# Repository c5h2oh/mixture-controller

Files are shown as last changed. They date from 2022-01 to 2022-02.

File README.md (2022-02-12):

# mixture-controller
RC engine mixture controller.

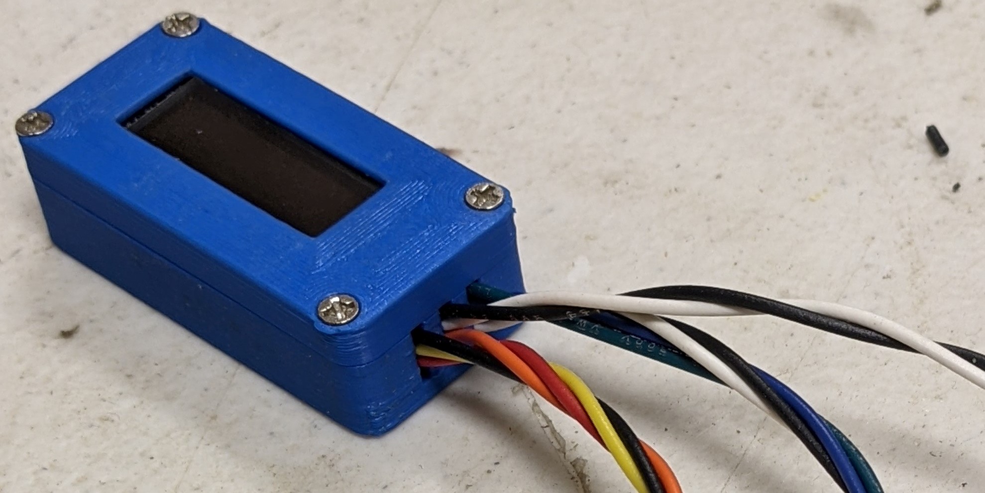
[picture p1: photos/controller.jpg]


This controller works with a stihl solenoid part number 0000 120 5111 and a custom solenoid housing (https://github.com/raleighcopter/mixture-controller/blob/main/photos/solenoid%20housing.pdf) to modulate gasoline flow to a conventional methanol carburator. This allows us to generate a custom fuel mixture curve on our transmitter that is slaved to the throttle channel output. The result is that we can vary the fuel:air mixture across the entire throttle range to make the engine run near stoichiometric fuel:air ratio at idle, full throttle, and every point in between. Without the solenoid and controller, our methanol engines run extremely rich in the middle. 

The controller takes an RC channel and maps a 1000 uS - 2000 uS channel pulse to a PWM solenoid pulse. Additionally, the controller measures atmospheric pressure and temperature and adjusts the fuel amount to maintain the ideal mixture regardless of the weather or altitude (which constantly changes as we fly our models). We have engines that were tuned at 85 degrees F that run just as well at 35 degrees F without touching the needles. 

I currently have my OS FT120-ii and Saito FA72 converted and Bert (the man behind the idea who designed the solenoid housing) has engines ranging from an asp 0.30 four stroke up to an ASP 1.6 boxer and a larger radial converted and running well. This conversion has been used on 2 stroke engines, 4 stroke engines, single  and twin cylinder engines and radial multi-cylinder engines.

I built the controller using a seeduino Xiao an IRLD110pbf MOSFET, a 2.2k resistor, a diode, a bmp280, and optionally, a 128x32 oled display and I've tested it on 4s NiMH and 2s LiFePo. Power comes in on the power and ground pads on the back of the Xiao. 

If you're powering your controller with a 2s LiFePo battery, wire a 1n4003 diode or something similar in the red wire before feeding power to the power pad or the Vcc pin. if you're powering your controller with a 4S NiMh, omit the diode.

The solenoid, bmp280, and optional display grab 3.3 volts from the Xiao's 3.3v pin. The MOSFET is wired to D3 and the RC channel is wired to D2. There's only 1 ground pad on the back and one ground pin so I doubled up on the pad on the back because I need 3 grounds.

I wired a 2.2k resistor across the MOSFET's gate and source (an 0805 smt resistor works really well here but a 1/8 watt resistor also works) and added a short piece of wire to those pins before I slipped some heat shrink over the separate pins. I soldered the wire that runs to the solenoid to the MOSFET's drain, trimmed the pins and then covered the entire MOSFET with heat shrink. After it was covered with heat shrink, I soldered the wire from the MOSFET's gate to D3 and the wire from the MOSFET's source to ground.

SDA and SCL from the bmp280 go to D4 and D5 and the optional display also uses these connections. if you measure resistance of about 10k between SDO and ground on the bmp280 it has a base address of 0x76. otherwise it has a base address of 0x77 and you need to change the base address at the top of the controller code. 

If you're building this with an oled display, wire the display to the same 4 points that the bmp280 is connected: 3.3v, ground, SDA, and SCL. You can wire it in parallel or in series with the bmp280.

if you're using this with an opentx transmitter and want s.port data, connect your s.port to pin 0 of the Xiao.

ebay/china is the least expensive source for bmp280 sensors at about $1 each and 128x32 oled displays at about $2.50. Be aware that we've seen fairly high failure rates on the China sourced bmp280 boards. As a result, the solenoid will signal a failed sensor at startup by buzzing for half a second and then remaining quiet for another half second and repeating indefinitely..

you'll need to install a few libraries in the arduino IDE: adafruit bmp280, adafruit ssd1306, adafruit GFX library and the frsky s.port sensor library by herman kruisman. you'll also need to add the seeeduino xiao board definition using the board manager.

build photos as well as parts lists and assembly instructions are on the wiki at https://github.com/raleighcopter/mixture-controller/wiki

Contact me at d.a.taylor.pe@gmail.com

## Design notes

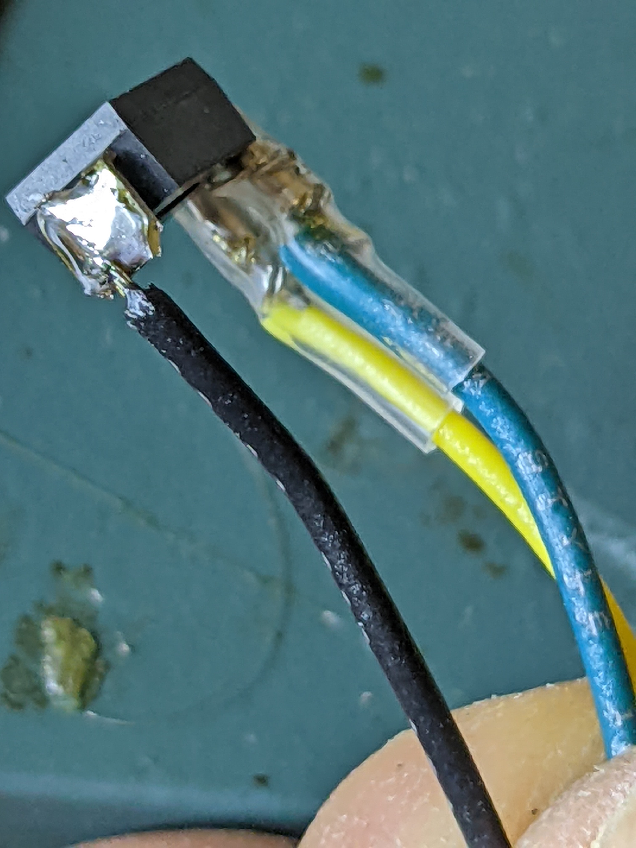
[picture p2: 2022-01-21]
photos/zero_11.jpg

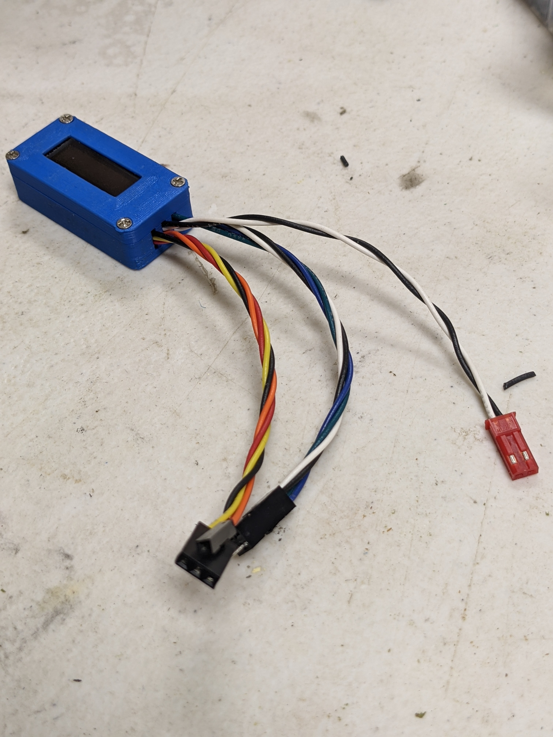
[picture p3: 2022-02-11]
photos/c1.jpg

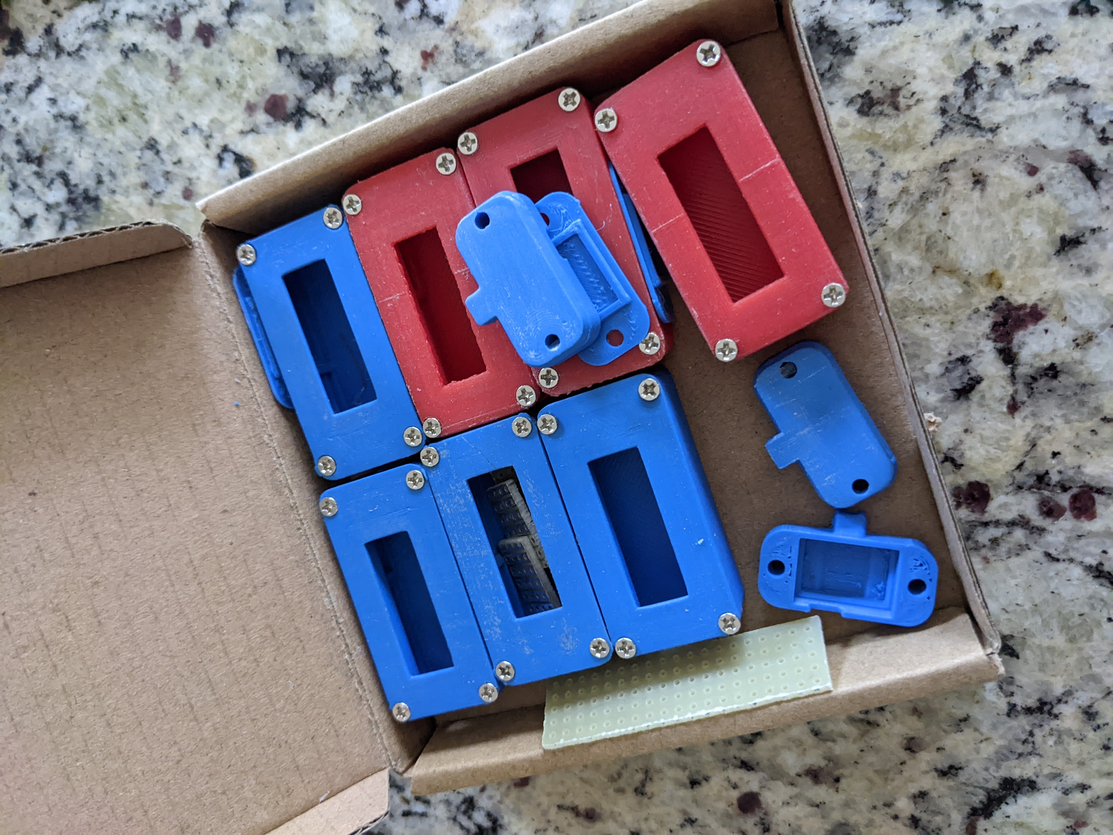
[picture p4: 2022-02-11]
photos/c2.jpg

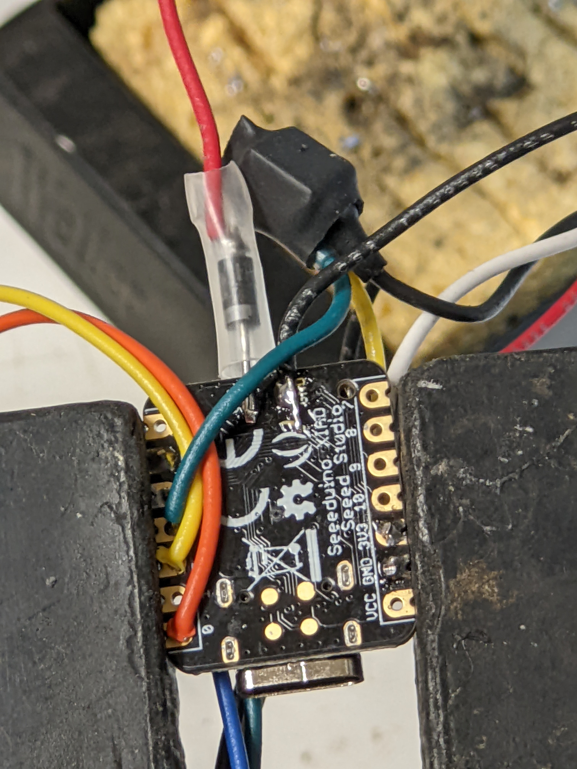
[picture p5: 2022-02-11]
photos/c12.jpg

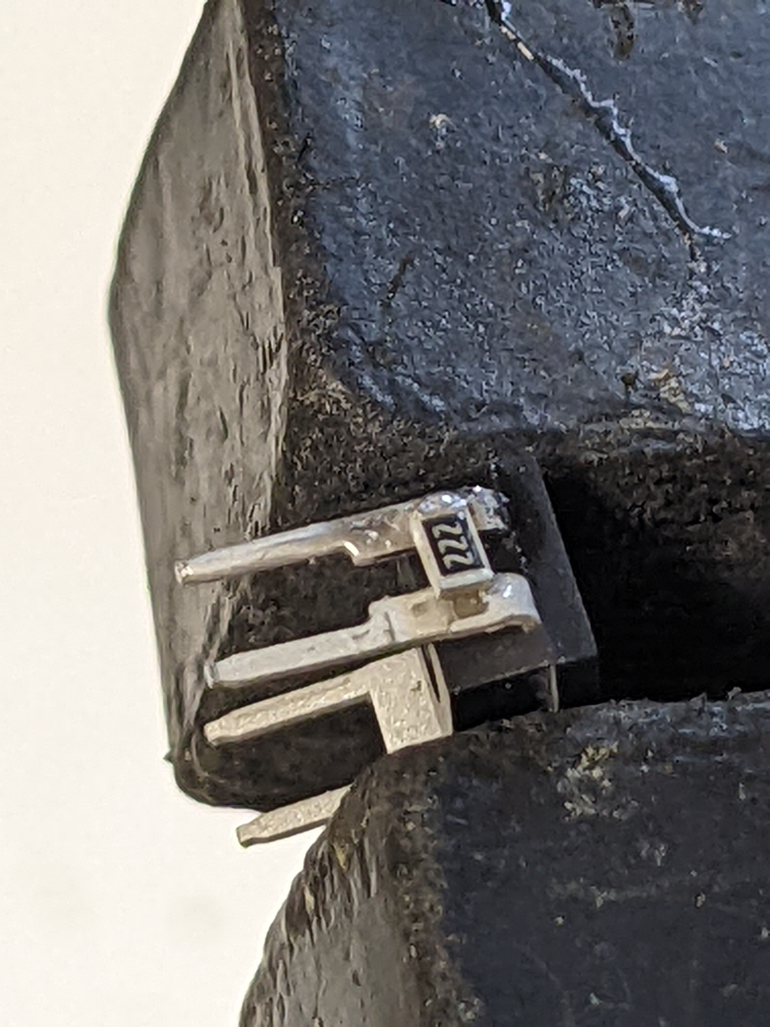
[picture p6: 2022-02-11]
photos/c4.jpg

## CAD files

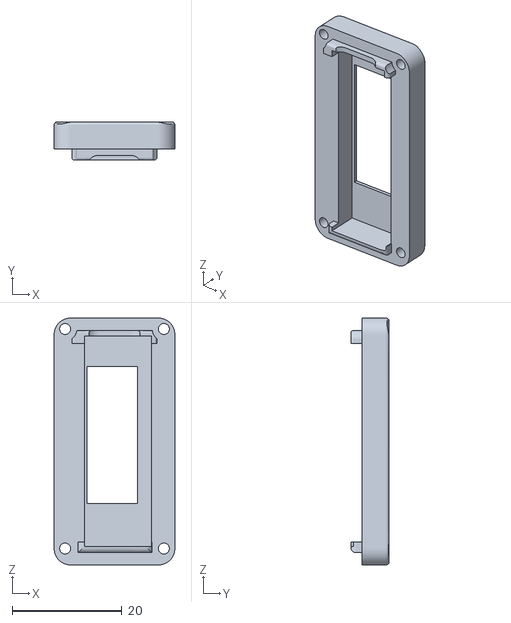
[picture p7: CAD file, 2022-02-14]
case_files/OLED lid.stl
22.0 x 7.00 x 45.0

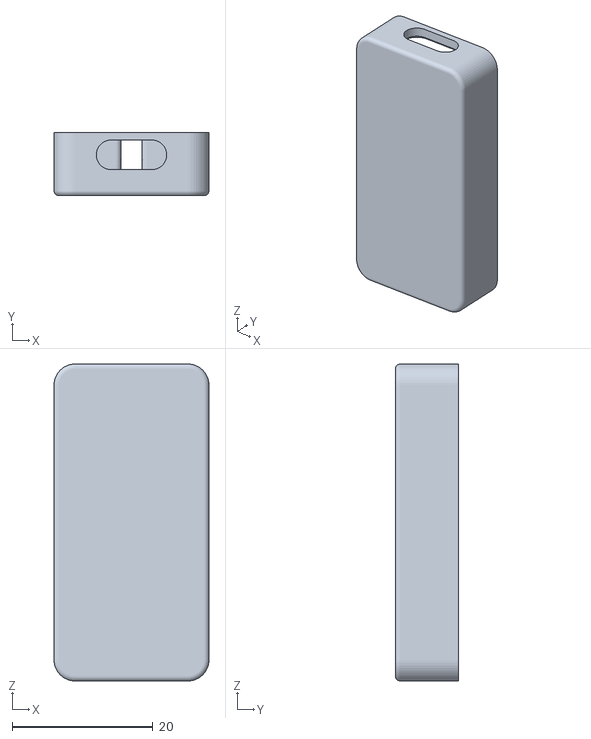
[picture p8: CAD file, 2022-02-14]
case_files/AMC case v9.stl
22.0 x 9.00 x 45.0

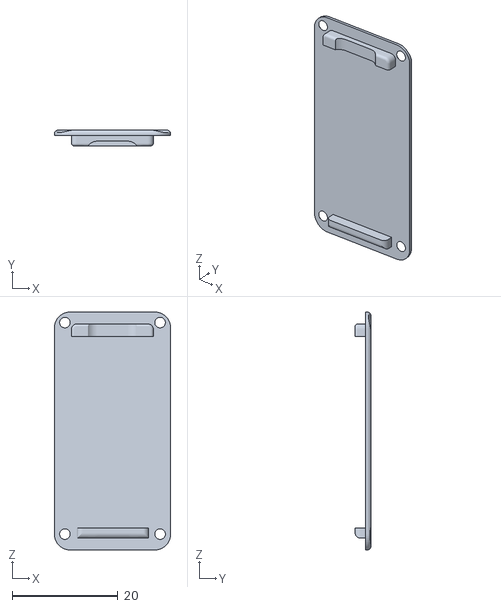
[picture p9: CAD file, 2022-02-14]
case_files/No OLED Lid.stl
22.0 x 3.00 x 45.0

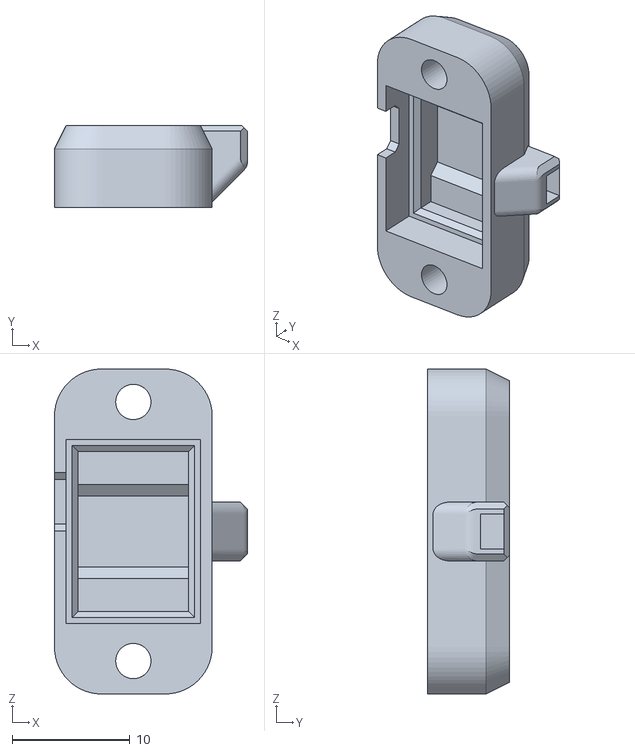
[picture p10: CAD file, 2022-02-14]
case_files/BMP280 Case.stl
16.4 x 7.00 x 27.6

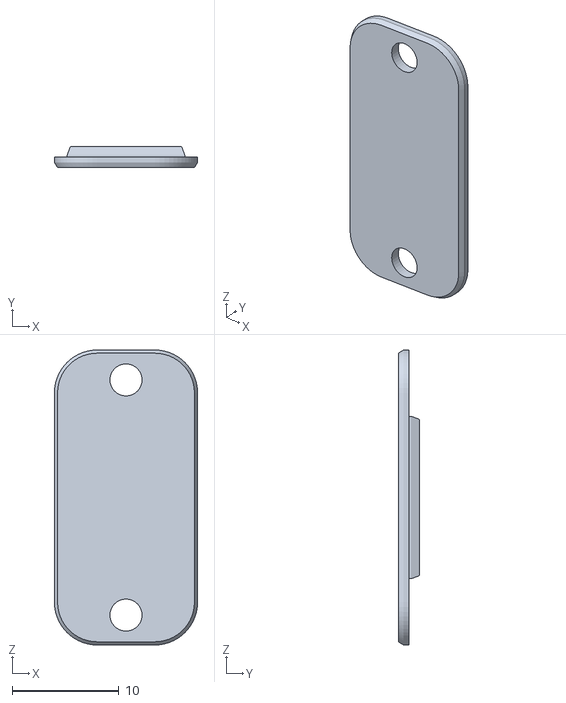
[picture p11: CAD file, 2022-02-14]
case_files/BMP280 cover.stl
13.4 x 2.00 x 27.6

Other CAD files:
case_files/AMC case.f3d

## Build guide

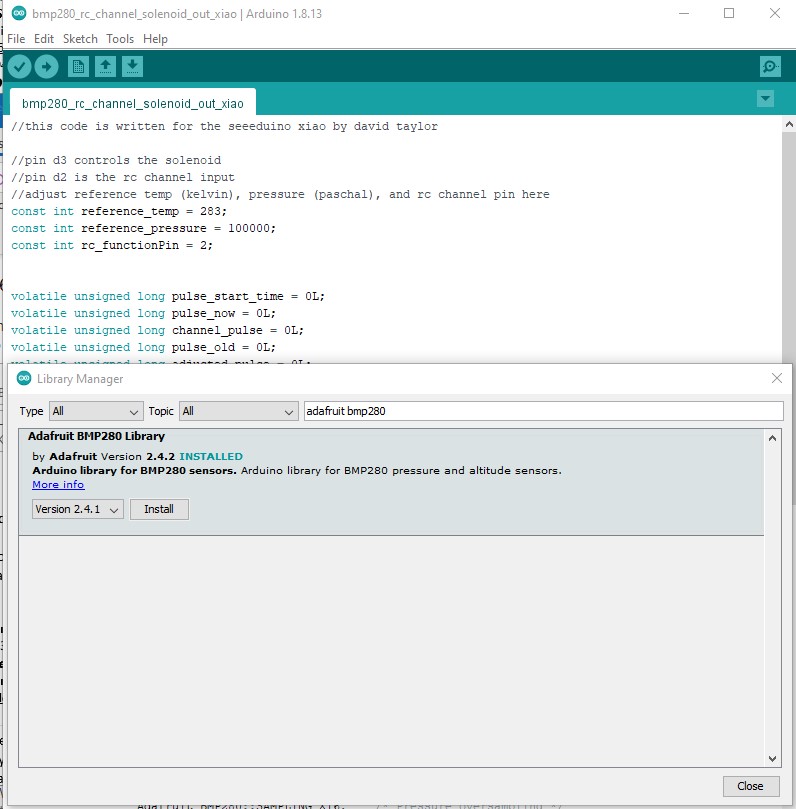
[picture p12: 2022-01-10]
photos/library install.jpg

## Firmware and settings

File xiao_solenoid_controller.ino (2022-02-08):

//this code is written for the seeeduino xiao by david taylor and released under the 
//GNU general public license V3.0. Permissions of this strong copyleft license are 
//conditioned on making available complete source code of licensed works and modifications,
//which include larger works using a licensed work, under the same license. Copyright and 
//license notices must be preserved. Contributors provide an express grant of patent rights.
// Also, Gary Cee from rcgroups is a douchebag

//pin d3 controls the solenoid
//pin d2 is the rc channel input
//adjust reference temp (kelvin), pressure (paschal), and rc channel pin here
const int reference_temp = 283;
const int reference_pressure = 100000;
const int rc_functionPin = 2;

//OLED addresses are 0x3C or 0x3D
#define OLED_ADDR   0x3C

//BMP280 addresses are 0x76 or 0x77
#define BMP280_ADDR   0x76

//****************************************************************************************
// **********************  DO NOT EDIT ANYTHING BELOW THIS LINE  *************************
//****************************************************************************************

unsigned long old_time;
int update_display;
const long display_interval = 1000; 
volatile unsigned long pulse_start_time = 0L;
volatile unsigned long pulse_now = 0L;
volatile unsigned long channel_pulse = 0L;
volatile unsigned long pulse_old = 0L;
volatile unsigned long adjusted_pulse = 0L;
volatile unsigned long solenoid_pulse = 0L;
volatile unsigned long usable_pulse = 0L;
int channel;
int bmp_error = 0;
char _buffer[9];

#include <SPort.h> 
#include <Wire.h>
#include <Adafruit_GFX.h>      // include Adafruit graphics library
#include <Adafruit_SSD1306.h>  // include Adafruit SSD1306 OLED display driver
#include <Adafruit_BMP280.h>   // include Adafruit BMP280 sensor library

Adafruit_BMP280 bmp; // I2C
Adafruit_SSD1306 display(-1);  // initialize Adafruit display library, share reset with xiao reset

SPortHub hub(0x12, 0);                    //Hardware ID 0x12, Software serial pin 0
CustomSPortSensor intake_temperature(getSensorData);  //Sensor with a callback function to get the data
CustomSPortSensor intake_pressure(getSensorData1);  //Sensor with a callback function to get the data
CustomSPortSensor compensation_ratio(getSensorData2);  //Sensor with a callback function to get the data
CustomSPortSensor solenoid_command(getSensorData3);  //Sensor with a callback function to get the data

void setup() {

  hub.registerSensor(intake_temperature);          //Add sensor to the hub
  hub.registerSensor(intake_pressure);             //Add sensor to the hub
  hub.registerSensor(compensation_ratio);          //Add sensor to the hub
  hub.registerSensor(solenoid_command);            //Add sensor to the hub


  hub.begin();                            //Start listening for s.port data

// initialize the SSD1306 OLED display with I2C address = 0x3C
  display.begin(SSD1306_SWITCHCAPVCC, OLED_ADDR);
// clear the display buffer.
  display.clearDisplay();
  display.setTextSize(1);   // text size = 1
  display.setTextColor(WHITE, BLACK);  // set text color to white and black background
  
//uncomment the next line to debug  
//SerialUSB.begin(115200);

  pinMode(rc_functionPin, INPUT);
  attachInterrupt(rc_functionPin, RCpinread, CHANGE);

  if (!bmp.begin(BMP280_ADDR, BMP280_CHIPID)) {
//  SerialUSB.println(F("Could not find a valid BMP280 sensor, check wiring or try a different address!"));
  bmp_error = 1;
  }
  
  bmp.setSampling(Adafruit_BMP280::MODE_NORMAL,     /* Operating Mode. */
                  Adafruit_BMP280::SAMPLING_X2,     /* Temp. oversampling */
                  Adafruit_BMP280::SAMPLING_X16,    /* Pressure oversampling */
                  Adafruit_BMP280::FILTER_X16,      /* Filtering. */
                  Adafruit_BMP280::STANDBY_MS_500); /* Standby time. */

//setup timer regisiters
  pinMode(3, OUTPUT);
  REG_GCLK_GENDIV = GCLK_GENDIV_DIV(1000) |       // Divide the main clock down by some factor to get generic clock
                    GCLK_GENDIV_ID(4);            // Select Generic Clock (GCLK) 4
  while (GCLK->STATUS.bit.SYNCBUSY);              // Wait for synchronization

  REG_GCLK_GENCTRL = GCLK_GENCTRL_IDC |           
                     GCLK_GENCTRL_GENEN |         // Enable GCLK4
                     GCLK_GENCTRL_SRC_DFLL48M |   // Set the 48MHz clock source
                     GCLK_GENCTRL_ID(4);          // Select GCLK4
  while (GCLK->STATUS.bit.SYNCBUSY);              // Wait for synchronization

// Enable the port multiplexer for the digital pin. 
  PORT->Group[g_APinDescription[3].ulPort].PINCFG[g_APinDescription[3].ulPin].bit.PMUXEN = 1;
  
//Connect the TCC0 timer to digital output - port pins are paired odd PMUO and even PMUXE 
  PORT->Group[g_APinDescription[2].ulPort].PMUX[g_APinDescription[2].ulPin >> 1].reg = PORT_PMUX_PMUXO_E; // | PORT_PMUX_PMUXE_F;

// Feed GCLK4 to TCC0 and TCC1
  REG_GCLK_CLKCTRL = GCLK_CLKCTRL_CLKEN |         // Enable GCLK4 to TCC0 and TCC1
                     GCLK_CLKCTRL_GEN_GCLK4 |     // Select GCLK4
                     GCLK_CLKCTRL_ID_TCC0_TCC1;   // Feed GCLK4 to TCC0 and TCC1
  while (GCLK->STATUS.bit.SYNCBUSY);              // Wait for synchronization

//Set for Single slope PWM operation: timers or counters count up to TOP value and then repeat
  REG_TCC1_WAVE |= TCC_WAVE_WAVEGEN_NPWM;        // Reverse the output polarity on all TCC0 outputs
  while (TCC1->SYNCBUSY.bit.WAVE);               // Wait for synchronization
 
  REG_TCC1_PER = 6144;                           // This sets the rate or frequency of PWM signal 
  while (TCC1->SYNCBUSY.bit.PER);                // Wait for synchronization
  
// Set the PWM signal to output 50% duty cycle initially 
  REG_TCC1_CC1 = 3072;                           // this sets the pwm duty cycle. values from 0 6145 are valid. 
  while (TCC1->SYNCBUSY.bit.CC1);                // Wait for synchronization

// Set prescaler and enable the outputs
  REG_TCC1_CTRLA |= TCC_CTRLA_PRESCALER_DIV1 |    // Divide GCLK4 by 1
                    TCC_CTRLA_ENABLE;             // Enable the TCC0 output
  while (TCC1->SYNCBUSY.bit.ENABLE);              // Wait for synchronization



}

//############################################################################

void loop() {

while(bmp_error == 1) {
  display.clearDisplay();
  display.setCursor(0, 0);
  display.setTextSize(2);
  display.println("  SENSOR");
  display.println("  ERROR");
  display.display();  
  REG_TCC1_CC1 = 3072;
  delay(500);
  REG_TCC1_CC1 = 0;
  delay(500);  
}
  
  hub.handle();                           //Handle new s.port data
  
//adjust for temp and pressure  
    adjusted_pulse = (usable_pulse * (reference_temp/(bmp.readTemperature()+273)*(bmp.readPressure()/reference_pressure))) * 6.145; 
    solenoid_pulse = constrain(adjusted_pulse, 0, 6145);
    solenoid_pulse = map(solenoid_pulse, 0, 6145, 6145, 0);

// load pulse value into timer register
    REG_TCC1_CC1 = (solenoid_pulse); 
    while (TCC1->SYNCBUSY.bit.CC1);

/*/  uncomment this section to debug  
    SerialUSB.print(bmp.readTemperature());
    SerialUSB.print(" *C     ");
    SerialUSB.print(bmp.readPressure());
    SerialUSB.print(" Pa     ");
    SerialUSB.print(adjusted_pulse);
    SerialUSB.print("  ");     
    SerialUSB.print(solenoid_pulse);
    SerialUSB.print("  ");
    SerialUSB.println(channel_pulse);
    SerialUSB.println(usable_pulse);
*/    
    


// do this once every display_interval.
  unsigned long current_time = millis();
  if(current_time - old_time >= display_interval){
    update_display = 1;                       //update the display

  if(update_display = 1){
    
// get temperature and pressure from library
  float temp     = bmp.readTemperature();   // get temperature
  float pressure = bmp.readPressure();      // get pressure
  float corr     = 100; 
// print data on the LCD

//clear the display
  display.clearDisplay();
  
// print temperature
  if(temp < 0)
    sprintf(_buffer, "-%02u.%01u C", (int)abs(temp), (int)(abs(temp) * 100) % 10 );
  else
    sprintf(_buffer, "%02u.%01u C", (int)temp, (int)(temp * 100) % 10 );
  display.setCursor(0, 0);
  display.setTextSize(1);
  display.print(_buffer);
 
// print degree symbol ( ° )
 if(temp < 0)
   display.drawCircle(32, 1, 1, WHITE);
 else
   display.drawCircle(26, 1, 1, WHITE);
   
// print pressure
  if(pressure < 100000)
    sprintf(_buffer, "%03u.%01u mB", (int)(pressure/100), (int)((uint32_t)pressure % 10));
  else
    sprintf(_buffer, "%04u.%01umB", (int)(pressure/100), (int)((uint32_t)pressure % 10));
  display.setCursor(0,8);
  display.setTextSize(1);
  display.print(_buffer);


//print correction
  
  corr =  1000 * (reference_temp/(temp+273)*(pressure/reference_pressure)); 
  if(corr<1000){
    sprintf(_buffer, "%02u.%01u", (int)(corr/10), (int)((uint32_t)corr % 10));
    display.setCursor(70,0);
    }
  else {
    sprintf(_buffer, "%03u.%01u", (int)(corr/10), (int)((uint32_t)corr % 10));
    display.setCursor(60,0);
    }
  display.setTextSize(2);
  display.print(_buffer);

// print a % symbol
  display.drawCircle(120, 1, 1, WHITE);
  display.drawCircle(123, 8, 1, WHITE);
  display.drawLine(123,1,120,8,WHITE);

//print channel pulse

  sprintf(_buffer, "%04u Channel Pulse", (int)(channel));
  display.setCursor(0,16);
  display.setTextSize(1);
  display.print(_buffer);  


// print solenoid pulse
  sprintf(_buffer, "%04u Solenoid Pulse", (int)(solenoid_pulse));
  display.setCursor(0,24);
  display.setTextSize(1);
  display.print(_buffer);  

// update the display
  display.display();

//reset the timer flag and set a new one
  old_time = millis();
  update_display=0;
}
}
}


// this function reads the rc channel pulse time
void RCpinread() {
  pulse_now = micros();
  pulse_old = channel_pulse;
  channel_pulse = pulse_now - pulse_start_time;
  pulse_start_time = pulse_now;
  if(channel_pulse < 988) {
    channel_pulse = pulse_old; //throw out low values
  }else if(channel_pulse > 2012) {
    channel_pulse = pulse_old; //throw out high values
  }
  channel_pulse = constrain (channel_pulse, 1000, 2000);
  channel = channel_pulse;
  usable_pulse = channel_pulse - 1000;
}

sportData getSensorData(CustomSPortSensor* intake_temperature) {
  sportData data; 
  data.applicationId = 0x5900;            //Set the sensor id for the current data poll. Set to 0 to discard the data, skip to the next sensor
  data.value = int(bmp.readTemperature()*10);                      //Set the sensor value 
  return data;
}

sportData getSensorData1(CustomSPortSensor* intake_pressure) {
  sportData data; 
  data.applicationId = 0x5901;            //Set the sensor id for the current data poll. Set to 0 to discard the data, skip to the next sensor
  data.value = int(bmp.readPressure()/10);                      //Set the sensor value 
  return data;
}

sportData getSensorData2(CustomSPortSensor* compensation_ratio) {
  sportData data; 
  data.applicationId = 0x5902;            //Set the sensor id for the current data poll. Set to 0 to discard the data, skip to the next sensor
  data.value = int(1000 * (reference_temp/(bmp.readTemperature()+273)*(bmp.readPressure()/reference_pressure)));                      //Set the sensor value 
  return data;
}

sportData getSensorData3(CustomSPortSensor* solenoid_command) {
  sportData data; 
  data.applicationId = 0x5903;            //Set the sensor id for the current data poll. Set to 0 to discard the data, skip to the next sensor
  data.value =  solenoid_pulse;                      //Set the sensor value 
  return data;
}

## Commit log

2022-01-03 solenoid controller with display and s.port telemetry
2022-01-05 added 1n4003 diode to power feed
2022-01-05 with diode
2022-01-05 wiring diagram with diode
2022-01-06 mixture controller for the arduino zero
    doesn't have s.port
    [zero_solenoid_controller.ino]
2022-01-07 fixed display of correction at 100%
    [zero_solenoid_controller.ino]
2022-01-08 More heat shrink
2022-01-10 omit diode for 4s nimh
2022-01-12 drawing of the solenoid housing (designed by bert van der schoor)
2022-01-12 solenoid housing drawing (by bert van der schoor)
2022-01-13 added solenoid pulse telemetry
2022-01-17 added schematic
2022-01-17 schematic drawing
2022-01-27 solenoid photos
2022-02-04 added sensor error signaling
    [zero_solenoid_controller.ino]
2022-02-08 Described failed sensor action.
2022-02-08 warn of sensor error
    when a sensor error occurs the solenoid will buzz repeatedly for half a second and then pause for half a second and the words "SENSOR ERROR" will be displayed on the display
    [zero_solenoid_controller.ino]
2022-02-11 3d printed case controller photos
2022-02-14 3d printed case files
    [AMC case v9.stl, AMC case.f3d, BMP280 Case.stl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]
